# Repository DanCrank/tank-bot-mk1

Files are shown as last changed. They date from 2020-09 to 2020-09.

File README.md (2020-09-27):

# tank-bot-mk1

A simple obstacle-avoiding vehicle.

Copyright (C) 2020 Dan Crank (danno@danno.org)

This program is free software: you can redistribute it and/or modify
it under the terms of the GNU General Public License as published by
the Free Software Foundation, either version 3 of the License, or
(at your option) any later version.

This program is distributed in the hope that it will be useful,
but WITHOUT ANY WARRANTY; without even the implied warranty of
MERCHANTABILITY or FITNESS FOR A PARTICULAR PURPOSE.  See the
GNU General Public License for more details.

You should have received a copy of the GNU General Public License
along with this program.  If not, see <https://www.gnu.org/licenses/>.

the vehicle is currently based on:
- [Adafruit Circuit Playground Bluefruit](https://www.adafruit.com/product/4333)
- [Adafruit Crickit](https://www.adafruit.com/product/3093)
- [RoboPeak RPLIDAR](https://www.adafruit.com/product/4010)
- [DFRobot Devastator tank chassis](https://www.dfrobot.com/product-1477.html) ([6V metal gear motor version](https://www.dfrobot.com/product-1476.html))

the Crickit is connected at its standard attachment points (see
https://learn.adafruit.com/adafruit-crickit-creative-robotic-interactive-construction-kit)

use of RPLIDAR requires the non-standard library https://github.com/robopeak/rplidar_arduino

IMPORTANT NOTE: at the time of this writing, the RPLidar Adruino library has a bug. The
RPLidar::begin method is declared to return bool but it does not actually return a value.
In my testing, this caused the controller to lock up. This can be fixed by editing the
files RPLidar.h and RPLidar.cpp and changing the RPLidar::begin method to return void in
both places.
 
the RPLIDAR is connected as generally described in the documentation (see
http://www.robopeak.net/data/doc/rplidar/appnote/RPLDAPPN01-rplidar_appnote_arduinolib-enUS.pdf)

| Pin | RPLIDAR | Circuit Playground |
|-----|---|---|
| 1 | GND | GND (any) |
| 2 | RX | TX |
| 3 | TX | RX |
| 4 | V5.0 | VOUT |
| 5 | GND | GND (any) |
| 6 | MOTOCTL | AUDIO* |
| 7 | VMOTO | VOUT |

NOTE: the circuit playground AUDIO pin is also passed through to
the speaker terminal on the crickit. do not connect anything to the
speaker terminal or it will interfere with RPLIDAR motor control.

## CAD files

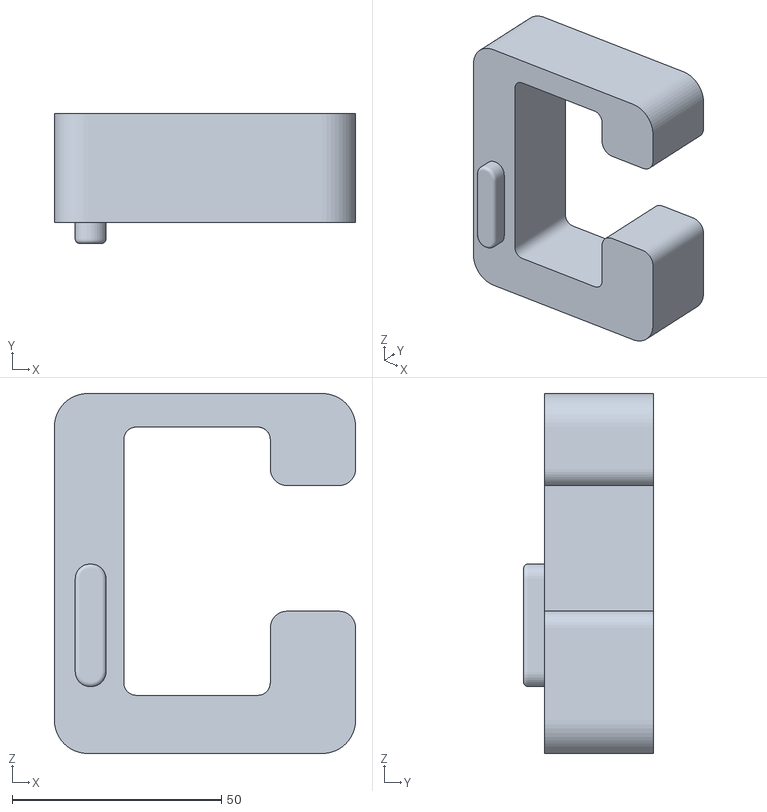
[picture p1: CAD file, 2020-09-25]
lidar-platform.stl
72.0 x 31.0 x 86.0

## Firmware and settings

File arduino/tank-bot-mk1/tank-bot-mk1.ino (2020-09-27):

/*
 * tank-bot-mk1.ino: controller for a simple obstacle-avoiding vehicle
 *
 * Copyright (C) 2020 Dan Crank (danno@danno.org)
 *
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
 * the vehicle is currently based on:
 *     Adafruit Circuit Playground Bluefruit
 *         https://www.adafruit.com/product/4333
 *     Adafruit Crickit
 *         https://www.adafruit.com/product/3093
 *     RoboPeak RPLIDAR
 *         https://www.adafruit.com/product/4010
 *     DFRobot Devastator tank chassis
 *         https://www.dfrobot.com/product-1477.html
 *         (this is the kit version that uses the 6V metal geared motors:
 *         https://www.dfrobot.com/product-1476.html)
 *
 * the Crickit is connected at its standard attachment points (see
 * https://learn.adafruit.com/adafruit-crickit-creative-robotic-interactive-construction-kit)
 *
 * use of RPLIDAR requires the non-standard library https://github.com/robopeak/rplidar_arduino
 * 
 * IMPORTANT NOTE: at the time of this writing, the RPLidar Adruino library has a bug. The
 * RPLidar::begin method is declared to return bool but it does not actually return a value.
 * In my testing, this caused the controller to lock up. This can be fixed by editing the
 * files RPLidar.h and RPLidar.cpp and changing the RPLidar::begin method to return void in
 * both places.
 * 
 *     void begin(HardwareSerial &serialobj);
 *
 * the RPLIDAR is connected as generally described in the documentation (see
 * http://www.robopeak.net/data/doc/rplidar/appnote/RPLDAPPN01-rplidar_appnote_arduinolib-enUS.pdf)
 *
 *     Pin              RPLIDAR                Circuit Playground
 *     1                GND                    GND (any)
 *     2                RX                     TX
 *     3                TX                     RX
 *     4                V5.0                   VOUT
 *     5                GND                    GND (any)
 *     6                MOTOCTL                AUDIO*
 *     7                VMOTO                  VOUT
 *
 *     * NOTE: the circuit playground AUDIO pin is also passed through to
 *     the speaker terminal on the crickit. do not connect anything to the
 *     speaker terminal or it will interfere with RPLIDAR motor control.
 */

#include <Adafruit_CircuitPlayground.h>
#include <Adafruit_Crickit.h>
#include <Adafruit_seesaw.h>
#include <seesaw_motor.h>
#include <RPLidar.h>

/*
 * globals
 */

RPLidar lidar;
const unsigned int RPLIDAR_MOTOR = 12;

// keep a global buffer representing the most recent scan of the surroundings
// each bin is a ten-degree segment (0-9.99, 10-19.99, etc.)
// if you want to use a different bin / buffer size, keep in mind that the
// code is currently optimized for an even number of bins and an even
// number of degrees in each bin. so good values of NAV_BUFFER_SIZE would
// be 18, 20, 30, 36, 60, 90, 180
struct nav_scan
{
  unsigned int distanceNear;
  unsigned int pointCount;
};
const unsigned int NAV_BUFFER_SIZE = 36;
nav_scan navBuffer[NAV_BUFFER_SIZE];

void initNavBuffer()
{
  debug("InitNavBuffer()");
  for (unsigned int i = 0; i < NAV_BUFFER_SIZE; i++)
  {
    navBuffer[i].distanceNear = 0;
    navBuffer[i].pointCount = 0;
  }
}

Adafruit_Crickit crickit;
seesaw_Motor motorLeft(&crickit);
seesaw_Motor motorRight(&crickit);
bool crickitStarted = false;

/*
 * status codes
 */
const unsigned int STATUS_INITIALIZING = 0;
const unsigned int STATUS_LIDAR_CONNECTING = 1;
const unsigned int STATUS_SCANNING = 2;
const unsigned int STATUS_MANEUVERING = 3;
const unsigned int STATUS_DRIVING = 4;
const unsigned int STATUS_HALT_TEMPORARY = 5;
const unsigned int STATUS_HALT_PERMANENT = 6;

unsigned int vehicleStatus = STATUS_INITIALIZING;

/*
 * failure codes (if these go higher than 9, status() will
 * need to be changed to display the code in binary; currently
 * it just lights the single neopixel for the code)
 */
const unsigned int FAIL_DEBUG = 0;                // SETUP_ONLY set, so we halt after setup()
const unsigned int FAIL_CRICKIT = 1;              // crickit.begin() failed - check power

/*
 * configuration values
 */

// uncomment this line for debugging over a tethered USB connection
// #define USB_DEBUG

// set to TRUE to halt after setup, for testing only
const bool SETUP_ONLY = false;

// threshold for calling a halt based on unsafe vehicle attitude (0.0 - 10.0)
// lower values will allow a steeper tilt before halting.
const float TILT_THRESHOLD = 7.0;

// brightness of the circuitplayground's built-in neopixel ring (used for
// indicating vehicle status); scale is 0 - 255 but it gets BRIGHT.
const unsigned int PIXEL_BRIGHTNESS = 16;

// maximum motor throttles (0.0 - 1.0). with the current setup this needs
// to be about 0.8 or less to avoid brownouts (even with the capacitor).
const float MOTOR_FORWARD = 0.8;
const float MOTOR_REVERSE = -0.8;

// size of the frontal cone to check for obstacles, specified in number of
// sectors off-center. for example, if this parameter is set to 2, then the
// sector immediately ahead of the vehicle and the 2 sectors on either side
// will be watched. to continue the example, if NAV_BUFFER_SIZE=36, each
// sector is 10 degrees, so the area watched ends up being 50 degrees (5*10).
const unsigned int NAV_AVOID_CONE = 2;

// distance (in mm) from an obstacle at which the vehicle will maneuver to
// avoid the obstacle
const unsigned int NAV_AVOID_DISTANCE = 500;

// distance (in mm) of free space that must exist on a potential escape route
// for the vehicle to consider that route.
const unsigned int NAV_ESCAPE_DISTANCE = 1000;

// setting to collect more than one complete LIDAR rotation in a "scan".
// this must be at least 1. values higher than 1 may help the vehicle make
// better maneuvering decisions, but interfere with the actual maneuvering
// because the time spent scanning extends the length of the decision-making
// cycle.
const unsigned int OVERSCAN = 1;

// LIDAR motor speed (0-255)
const unsigned int LIDAR_MOTOR_SPEED = 255;

// minimum distance, inside which LIDAR data points are thrown out. this is
// used to filter out spurious data points at unreasonably close distances
// (inside the perimeter of the vehicle or thereabouts). value in mm.
// the datasheet lists minimum measurable distance as 150mm, so that's a
// good initial value.
const unsigned int LIDAR_MINIMUM_DISTANCE = 150;

// minimum quality, beneath which LIDAR data points are thrown out. this is
// a score assigned by the device, and its meaning is not documented (it is
// an unsigned byte coming from the device). in practice, most data points
// are observed to be quality = 15.
const unsigned int LIDAR_MINIMUM_QUALITY = 12;

/*
 * vehicle status functions
 */

const unsigned int NUM_PIXELS = 10;
const uint32_t WHITE = 0x00FFFFFF;
const uint32_t RED = 0x00FF0000;
const uint32_t GREEN = 0x0000FF00;
const uint32_t BLUE = 0x000000FF;
const uint32_t YELLOW = 0x00FF8800;
const uint32_t CYAN = 0x0000FFFF;
const uint32_t PURPLE = 0x008800FF;
const uint32_t BLACK = 0x00000000;

void setStatus(unsigned int newStatus, int failCode = -1)
{
  // set a status indicator of the appropriate color
  // each time status() is called, the lit pixel will move one position
  // clockwise around the ring, as an indicator that the control loop is
  // still running. if status is HALT_PERMANENT, the entire ring will
  // light red.
  static unsigned int statusPosition = 0;

  if (newStatus == vehicleStatus) return;
  vehicleStatus = newStatus;
  if (vehicleStatus == STATUS_HALT_PERMANENT)
  {
    debug("status: STATUS_HALT_PERMANENT");
    // for a permanent halt, light the ring up red
    // and set one position white as a fault code
    for (unsigned int i = 0; i < NUM_PIXELS; i++)
      if (i == failCode) CircuitPlayground.setPixelColor(i, WHITE);
      else CircuitPlayground.setPixelColor(i, RED);
    fullStop();
    // main control loop will recognize the halt status
  } else {
    CircuitPlayground.clearPixels();
    uint32_t color;
    switch (vehicleStatus)
    {
      case STATUS_DRIVING: color = GREEN; debug("status: STATUS_DRIVING"); break;
      case STATUS_HALT_TEMPORARY: color = YELLOW; debug("status: STATUS_HALT_TEMPORARY"); break;
      case STATUS_INITIALIZING: color = WHITE; debug("status: STATUS_INITIALIZING"); break;
      case STATUS_LIDAR_CONNECTING: color = PURPLE; debug("status: STATUS_LIDAR_CONNECTING"); break;
      case STATUS_SCANNING: color = CYAN; debug("status: STATUS_SCANNING"); break;
      case STATUS_MANEUVERING: color = BLUE; debug("status: STATUS_MANEUVERING"); break;
    }
    CircuitPlayground.setPixelColor(statusPosition, color);
    statusPosition = (statusPosition + 1) % NUM_PIXELS;
  }
}

void neopixelInit()
{
  debug("neopixelInit()");
  CircuitPlayground.clearPixels();
  // initialization display
  for (unsigned int i = 0; i < NUM_PIXELS; i++)
  {
    CircuitPlayground.setPixelColor(i, GREEN);
    delay(250);
  }
  for (unsigned int i = 0; i < NUM_PIXELS; i++)
  {
    CircuitPlayground.setPixelColor(i, BLACK);
    delay(250);
  }
  setStatus(STATUS_INITIALIZING);
}

// shut down all moving parts
void fullStop()
{
  debug("fullStop()");
  // shut down LIDAR motor
  analogWrite(RPLIDAR_MOTOR, 0);
  // shut down drive motors
  driveStop();
}

// shut down but go into a check loop to wait for soft-reset
// caller should return to main loop after calling this function
void haelp()
{
  if (vehicleStatus != STATUS_HALT_PERMANENT)
  {
    setStatus(STATUS_HALT_TEMPORARY);
    driveStop();
    // wait for a start-button press to return to main loop
    while (true)
    {
      if (CircuitPlayground.leftButton()) return;
      delay(200);
    }
  }
}

/*
 * drive motor functions
 */
void driveInit()
{
  debug("driveInit()");
  if (!crickit.begin())
  {
    setStatus(STATUS_HALT_PERMANENT, FAIL_CRICKIT);
  } else {
    crickitStarted = true;
    motorLeft.attach(CRICKIT_MOTOR_A1, CRICKIT_MOTOR_A2);
    motorRight.attach(CRICKIT_MOTOR_B1, CRICKIT_MOTOR_B2);
    setStatus(STATUS_INITIALIZING);
  }
}

void driveForward()
{
  debug("driveForward()");
  if (crickitStarted)
  {
    motorLeft.throttle(MOTOR_FORWARD);
    motorRight.throttle(MOTOR_FORWARD);
  }
}

void driveReverse()
{
  debug("driveReverse()");
  if (crickitStarted)
  {
    motorLeft.throttle(MOTOR_REVERSE);
    motorRight.throttle(MOTOR_REVERSE);
  }
}

void driveRotateRight()
{
  debug("driveRotateRight()");
  if (crickitStarted)
  {
    motorLeft.throttle(MOTOR_FORWARD);
    motorRight.throttle(MOTOR_REVERSE);
  }
}

void driveRotateLeft()
{
  debug("driveRotateLeft()");
  if (crickitStarted)
  {
    motorLeft.throttle(MOTOR_REVERSE);
    motorRight.throttle(MOTOR_FORWARD);
  }
}

void driveStop()
{
  debug("driveStop()");
  if (crickitStarted)
  {
    motorLeft.throttle(0.0);
    motorRight.throttle(0.0);
  }
}

/*
 * LIDAR functions
 */

// note: lidarInit only sets up the serial port and motor control.
// it does not actually attempt any communication with the device.
void lidarInit()
{
  debug("lidarInit()");
  lidar.begin(Serial1);
  pinMode(RPLIDAR_MOTOR, OUTPUT);
  analogWrite(RPLIDAR_MOTOR, 0);
  setStatus(STATUS_INITIALIZING);
}

// handshake with the lidar device and start scanning.
// return TRUE if connection was successful, FALSE otherwise.
bool lidarConnect()
{
  debug("lidarConnect()");
  setStatus(STATUS_LIDAR_CONNECTING);
  // try to detect RPLIDAR
  rplidar_response_device_info_t info;
  if (IS_OK(lidar.getDeviceInfo(info)))
  {
    debug("lidar.getDeviceInfo OK model=" + String(info.model) + " firmware_version=" + String(info.firmware_version) + " hardware_version=" + String(info.hardware_version));
    if (IS_OK(lidar.startScan()))
    {
      debug("lidar.startScan OK, starting motor");
      // start motor rotating
      analogWrite(RPLIDAR_MOTOR, LIDAR_MOTOR_SPEED);
      delay(1000);
      return true;
    }
  }
  debug("lidarConnect() FAILED!");
  return false;
}

// take one (or more) complete scans of the surroundings and update the buffer
// return TRUE if the buffer is updated, FALSE if there was a problem
// and we have to stop to re-connect to the LIDAR.
bool lidarScan()
{
  unsigned long startTime = millis();
  debug("lidarScan()");
  //derive a couple of unchanging values, for a bit of efficiency
  static unsigned int binSize = 360 / NAV_BUFFER_SIZE;
  static unsigned int halfABin = binSize / 2;
  initNavBuffer();
  unsigned int pointsCollected = 0;
  unsigned int pointsThrownOut = 0;
  unsigned int startBits = 0;
  setStatus(STATUS_SCANNING);
  while (true)
  {
    // wait for a data point
    if (IS_OK(lidar.waitPoint()))
    {
      RPLidarMeasurement point = lidar.getCurrentPoint();
      // we want this function to be fast - therefore round off the floating point values first thing
      unsigned int theAngle = round(point.angle);
      unsigned int theDistance = round(point.distance);
      if (point.startBit)
      {
        startBits++;
        if (startBits > OVERSCAN)
        {
          //finish the scan
          debug("Scan complete; " + String(pointsCollected) + " points collected, " + String(pointsThrownOut) + " thrown out");
          debug("Scan took " + String(millis() - startTime) + " milliseconds at overscan=" + OVERSCAN);
          return true;
        }
      }
      if ((point.quality >= LIDAR_MINIMUM_QUALITY) && (theDistance > LIDAR_MINIMUM_DISTANCE)) // filter out bad data points
      {
        pointsCollected++;
        // normalize the heading
        // with the current mounting, "forward" is the direction reported by the lidar as
        // 90 degrees. we need that to be stored as 180 degrees (putting that in the middle
        // of the range makes the buffer indexing simpler).
        theAngle += 90;
        if (theAngle >= 360) theAngle -= 360;
        // consolidating the awkwardness here: to make navigation somewhat better, we want
        // "straight ahead" to be in the center of a bin, not on the dividing line between
        // two bins. So navBuffer[0] is going to be directly aft and
        // navBuffer[NAV_BUFFER_SIZE/2] will be directly forward.
        unsigned int bin = (unsigned int)((theAngle + halfABin) / binSize);
        if (bin == NAV_BUFFER_SIZE) bin = 0;  // awkward wrap around conversion
        // save the nearest blip in each bin for obstacle detection
        if ((navBuffer[bin].pointCount == 0) || (point.distance < navBuffer[bin].distanceNear))
          navBuffer[bin].distanceNear = point.distance;
        navBuffer[bin].pointCount++;
      } else pointsThrownOut++;
    } else {
      // here if there's an error; return FALSE so the control loop
      // can stop the vehicle and recover
      debug("lidarScan() timed out while waiting for data point");
      return false;
    }
  }
}

// old demo code that displayed the heading to the nearest object as a red light
// on the circuitplayground neopixel ring - no longer used, but keeping it as an example
//void lidarDemo()
//{
//  if (IS_OK(lidar.waitPoint()))
//  {
//    status(STATUS_OK);
//    float distance = lidar.getCurrentPoint().distance; //distance value in mm
//    float angle    = lidar.getCurrentPoint().angle; //angle value in degrees
//    bool  startBit = lidar.getCurrentPoint().startBit; //whether this point belongs to a new scan
//    byte  quality  = lidar.getCurrentPoint().quality; //quality of the current measurement
//
//    //test! find the nearest object in the current scan and mark it with a red neopixel
//    //don't know yet what angle value corresponds to what vehicle heading
//    if (startBit)
//    {
//      // normalize the heading - 90 degrees is forward
//      theAngle -= 90.0;
//      if (theAngle < 0.0) theAngle += 360.0;
//      // figure out which pixel corresponds to this angle
//      // pixels are numbered counterclockwise 0-9
//      // with current mounting, a 0 degree heading is between 4 and 5
//      int iDirIndex = 0;
//      iDirIndex = (int)(4.5 - (theAngle / 36.0));
//      if (iDirIndex < 0) iDirIndex += 10;
//      CircuitPlayground.clearPixels();
//      CircuitPlayground.setPixelColor(iDirIndex, RED);
//      //Serial.println("Angle=" + String(theAngle) + " Distance=" + String(theDistance) + " Quality=" + String(theQuality) + " Points=" + String(iPointCount) + " Index=" + String(iDirIndex));
//      theAngle = 0.0;
//      theDistance = 10000.0;
//      theQuality = 0;
//      iPointCount = 0;
//    }
//    // quality score appears to be a max of 15, but seems to get enough 15s
//    // that we can throw everything else out. we also seem to get a lot of
//    // spurious data points at 0 distance - filter them out too
//    if ((quality >= 15) && (distance > 0.0))
//    {
//      if (distance < theDistance)
//      {
//        theDistance = distance;
//        theAngle = angle;
//        theQuality = quality;
//      }
//      iPointCount++;
//    }
//  } else {
//    lidarConnect();
//  }  
//}

/*
 * navigation / obstacle-avoidance functions
 */

// return the bin index of the nearest obstruction, or -1 if no obstructions are visible
// inside the NAV_AVOID_CONE and within NAV_AVOID_DISTANCE millimeters.
int navFindObstruction(int sector = (NAV_BUFFER_SIZE / 2), int distance = NAV_AVOID_DISTANCE)
{
  debug("navFindObstruction()");
  int bin = -1;
  unsigned int range = distance + 1;
  for (int i = sector - NAV_AVOID_CONE; i <= sector + NAV_AVOID_CONE; i++)
  {
    int realIndex = (i + NAV_BUFFER_SIZE) % NAV_BUFFER_SIZE;  // handle indexes that span buffer boundaries
    if (navBuffer[realIndex].pointCount == 0)
    {
      debug("I have no data for sector " + String(i) + ", declaring that sector obstructed.");
      //bin = realIndex;
      //range = 0;
    } else if ((navBuffer[realIndex].distanceNear < distance) &&
             (navBuffer[realIndex].distanceNear < range)) {
      bin = realIndex;
      range = navBuffer[realIndex].distanceNear;
    }
  }
  if (bin == -1)
    debug("No obstruction detected");
  else
    debug("Nearest obstruction detected in sector " + String(bin) + ", range=" + String(range) + "mm");
  return bin;
}

// look at the entire nav buffer (360 degrees) and find the best escape route
// from the given obstruction, or -1 if no escape can be found
int navFindEscape()
{
  debug("navFindEscape()");
  int bin = -1;
  int bestScore = NAV_BUFFER_SIZE / 2;
  for (int i = 0; i < NAV_BUFFER_SIZE; i++)
  {
    // for each bin, score it as a possible escape.
    // determine the number of sectors we would have to turn to reach this heading
    int deviation = (NAV_BUFFER_SIZE / 2) - i;  // halfway point of the buffer is straight ahead
    deviation = abs(deviation);  // arduino reference says not to nest operations inside abs()
    // check to see if the current buffer would read as unobstructed if the vehicle were pointed
    // to the heading being evaluated. if yes, the route gets a score by its deviation (lower
    // being better) and we keep the lowest score.
    if ((navFindObstruction(i, NAV_ESCAPE_DISTANCE) == -1) && (deviation < bestScore))
    {
      debug("New high score: sector " + String(i) + " deviation=" + String(deviation));
      bin = i;
      bestScore = deviation;
    }
  }
  if (bin == -1) debug("No escape found.");
  return bin;
}

// based on the current nav buffer, rotate to the best escape heading.
// return true if the vehicle is now pointed in a good direction,
// false if not...except that losing the lidar connection will still
// return true, because we don't want to TEMPORARY_HALT in that case.
bool navEscape()
{
  debug("navEscape()");
  driveStop();
  // find the escape route
  int escape = navFindEscape();
  if (escape == -1)
  {
    // oh noes, no escape can be found
    debug("No escape found, navEscape returning FALSE");
    return false;
  } else if (escape == (NAV_BUFFER_SIZE / 2)) {
    // special case: navFindEscape told us to go the direction we were already going...
    // since navFindEscape isn't supposed to refresh the buffer, this probably means
    // something is confused
    debug("navFindEscape returned sector " + String(escape) + ", current heading? navEscape returning TRUE");
    return true;
  } else {
    // figure out if we're turning left or right, then start turning
    if (escape < (NAV_BUFFER_SIZE / 2)) driveRotateLeft();
    else driveRotateRight();
    while (true)
    {
      if (!situationCheck()) return false;
      // re-scan
      if (!lidarScan())
      {
        // scan error
        // return true here so main loop can try to reconnect and recover
        debug("LIDAR timeout - navEscape returning TRUE to attempt reconnect");
        return true;
      }
      // check for clear road ahead
      if (navFindObstruction() == -1) return true;  // get in losers
      // otherwise keep looking
    }
  }
}

/*
 * situation check functions
 */
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
void loop()
{
  // MAIN CONTROL LOOP
  unsigned long newClock = millis();
  debug("loop() [last loop took " + String(newClock - loopClock) + "ms]");
  loopClock = newClock;
  // check to see if vehicle has halted
  if (vehicleStatus == STATUS_HALT_PERMANENT)
  {
    delay(2000);
    return;
  }
  // check to see if vehicle has capsized, been picked up, etc.
  if (!situationCheck())
  {
    haelp();
    return;
  }

  // scan the surroundings
  debug("***MAIN CONTROL LOOP***");
  if (lidarScan())
  {
    int obstruction = navFindObstruction();
    if (obstruction == -1)
    {
      debug("No obstacles ahead - driving forward.");
      // no obstacles ahead, start moving forward
      setStatus(STATUS_DRIVING);
      driveForward();
    } else {
      debug("Obstacle detected in sector " + String(obstruction) + ", stopping.");
      driveStop();
      // turn to a new heading
      setStatus(STATUS_MANEUVERING);
      bool ok = navEscape();
      if (!ok)
        // here if there was a problem during maneuvering
        // so wait to be rescued
        haelp();
    }
  } else {
    // LIDAR error...stop and try to reconnect
    debug("LIDAR error (main loop)...attempting to reconnect");
    driveStop();
    lidarConnect();
  }
}

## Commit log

2020-09-25 initial commit.
    [lidar-platform.stl]
2020-09-27 second round of testing and tuning
    This version uses a much simpler maneuvering algorithm, as
    the approach initially taken doesn't work too well.
    This approach is still sensitive to the amount of time it
    takes to acquire LIDAR data. The device runs at about 3 Hz,
    so at overscan=3 it takes about a second to run lidarScan().
    This means the decision-making loop for stopping a turn will
    often overshoot the heading it's looking for. overscan=1
    seems to work best even though it may give ragged data.
    [tank-bot-mk1.ino]
